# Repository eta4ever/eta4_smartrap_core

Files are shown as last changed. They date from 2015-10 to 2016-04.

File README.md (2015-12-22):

Ремикс, ремейк, форк, или как там это называется 3D-принтера Smartrap Core v.1.2 (https://www.youmagine.com/designs/smartcore). Основная идея - использование 15-миллиметрового алюминиевого квадрата в качестве рамы. 

Надо делать боковые стенки. Как минимум с боков, а лучше еще и сзади и снизу и вообще все закрывать. Или не надо, делаю откосины.

Что касается прошивки: взят релиз Marlin, актуальный на ноябрь 2015. Настроен на CoreXY, 190x190x190, по X и Y ремни GT2, на Z шпилька М5, экструдер МК8, все драйверы 1/16. Плюс Reprap Discount Full Graphic Controller.

Девайсина работает, обзор: http://3dtoday.ru/blogs/eta4ever/kubocore-my-variation-smartcore/

----------

2015-12-22

Корпус под плату, укладка проводов, фанерное дно, вулкан.
Обзор: http://3dtoday.ru/blogs/eta4ever/kubocore-part-3/

----------

2015-12-16

Направляющие Z на 110 мм, откосины на боковины по две штуки (профиль длиной 180 мм, угловые соединители 45.stl в Frame). Стало почти отлично.
Обзор доработок http://3dtoday.ru/blogs/eta4ever/kubocore-progress/

----------

2015-11-17

Соорудил стол на большой консоли. Стало лучше, но все равно хлипко. Надо шире расставлять направляющие (сейчас 60 мм, на консоли предусмотрено под 110 мм), а в идеале - делать направляющие с двух сторон. Но это гемор.

----------

2015-11-14

Реально печатная область сейчас получается 175х140 всего лишь. По Y в процессе доработки, будет побольше. Надо было длиннее раму делать, ну, поэкономил копеечный люминь, блин.

Напечатал новую консольку (Custom - Z - carriage), она монументальная. Пока что в процессе внедрения, примеряюсь к ней с уголками.

Ну и держалка для движка подачи пластика (Custom - extruder drive mount). А то надоело, что движок на стяжке болтается.

-----------

----------

Remix, remake or fork of Smartrap Core v.1.2 (https://www.youmagine.com/designs/smartcore).

----

Frame - уголки для сборки рамы из люминя.  Frame corners.

XY - переделанные крепления двигателей и роликов XY. Modified XY motors and rollers mounts. xy_left, xy_right, xy2_left_right

Z - переделанные детали Z. Под шпильку, из предыдущей версии Smartrap Core 1.01, с переделками под TR8x8. Modified Z parts, taken from previous 1.01 (threaded) version of Smartrap core, adapted for TR8x8 nut and bolt. z_carriage, z_top, z_bottom.

Unmodified - не затронутые переделками оригинальные детали, выгруженные из OpenJSCAD и пропущенные через netfabb для Slic3r. Untouched parts exported from OpenJSCAD and repaired in netfabb for Slic3r.

Алярма: Y Axis из Unmodified печатается с поддержкой, чтобы горизонтальные разрезы получились. Ну, они потом получаются, ножом и надфилем. Или можно стоя, но тоже с поддержкой под зажим линейного подшипника.

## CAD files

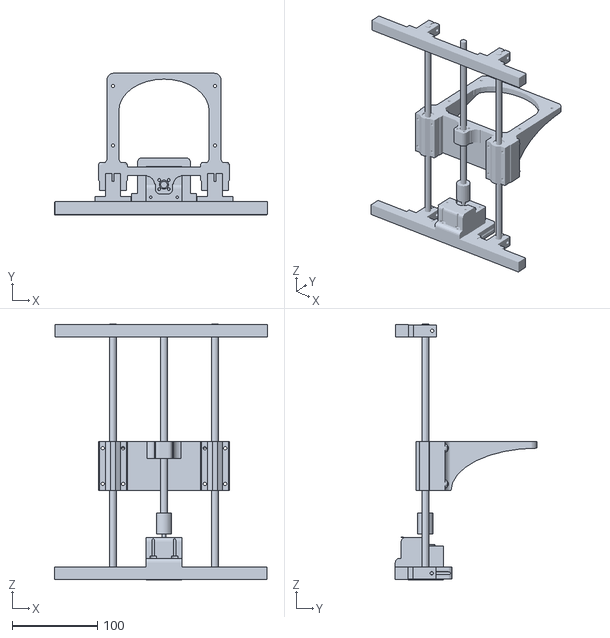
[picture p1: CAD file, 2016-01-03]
Custom/Z-experimental/z-assembly.stl
251.0 x 166.5 x 301.0

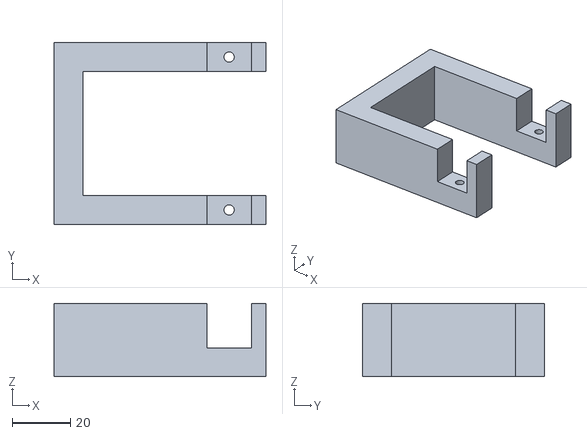
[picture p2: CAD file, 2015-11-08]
Custom/extruder drive mount.stl
72.5 x 62.3 x 25.0

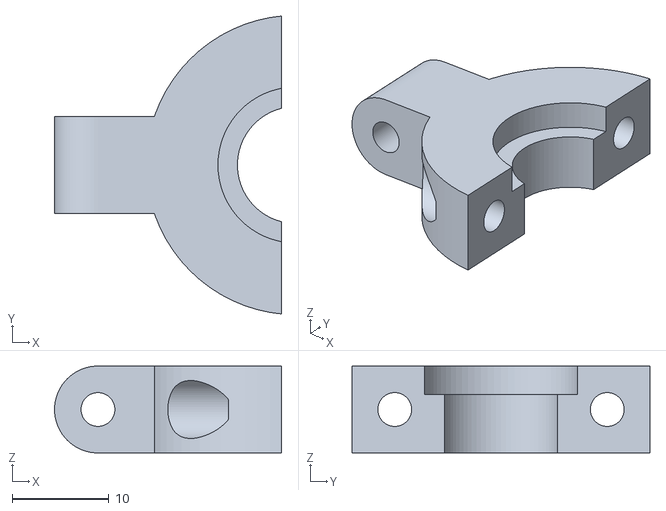
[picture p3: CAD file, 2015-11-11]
Custom/head/mount2_printable-only clip.stl
23.5 x 30.8 x 9.00

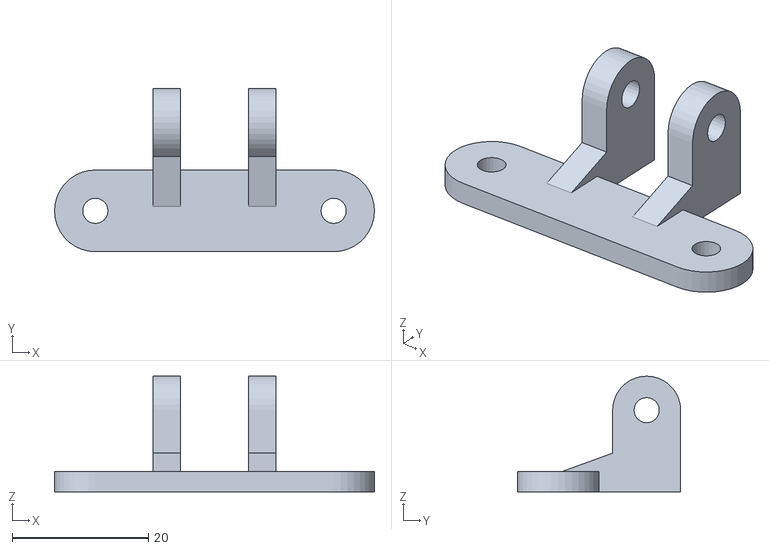
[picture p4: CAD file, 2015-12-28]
Custom/head/side_blower/side_blower_mount.stl
47.0 x 24.0 x 17.0

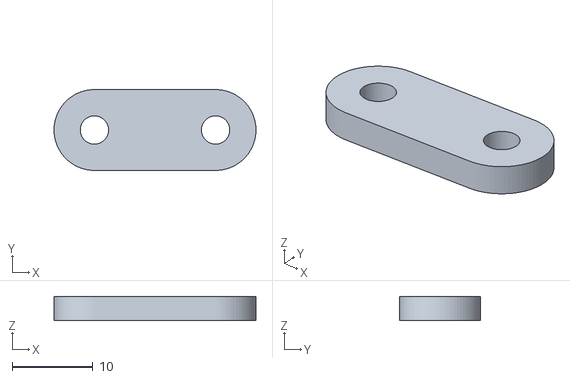
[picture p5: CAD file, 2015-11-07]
Custom/head/side_cooler_40mm/side_cooler_plank.stl
25.0 x 10.0 x 3.00

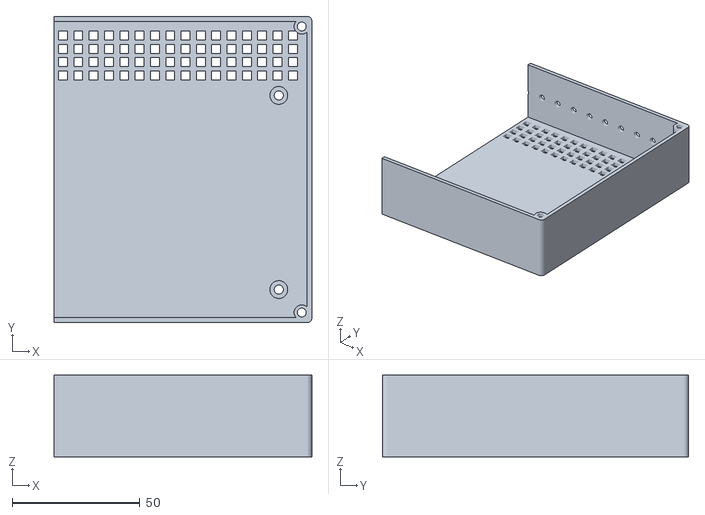
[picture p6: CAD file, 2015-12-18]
Custom/mks gen box/mks gen box1.stl
101.0 x 120.0 x 32.0

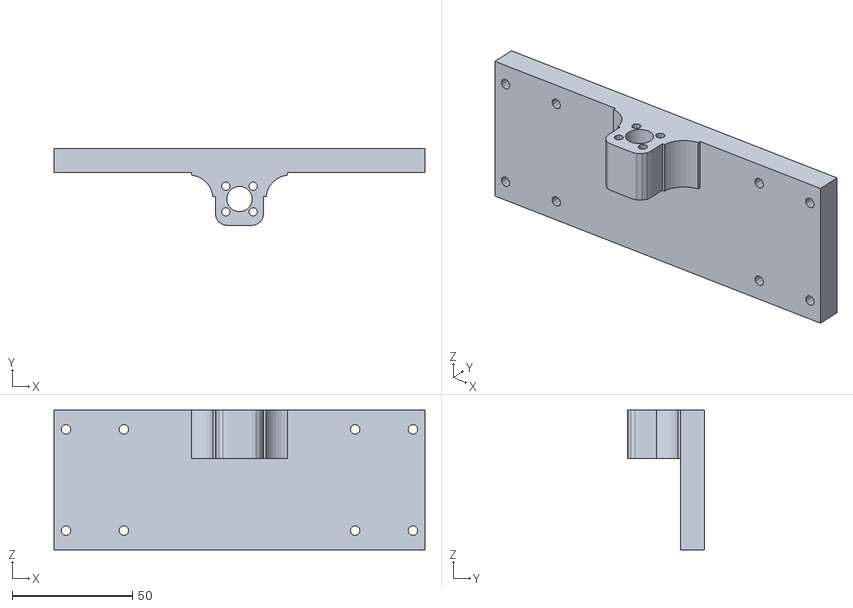
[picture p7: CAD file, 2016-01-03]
Custom/Z-experimental/z-plank.stl
154.0 x 32.0 x 58.0

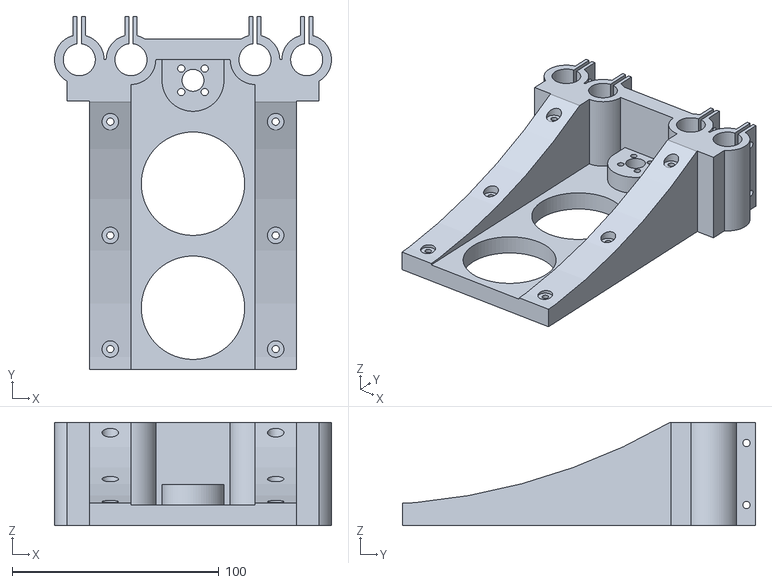
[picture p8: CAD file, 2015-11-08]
Custom/Z/carriage.stl
134.0 x 171.0 x 50.0

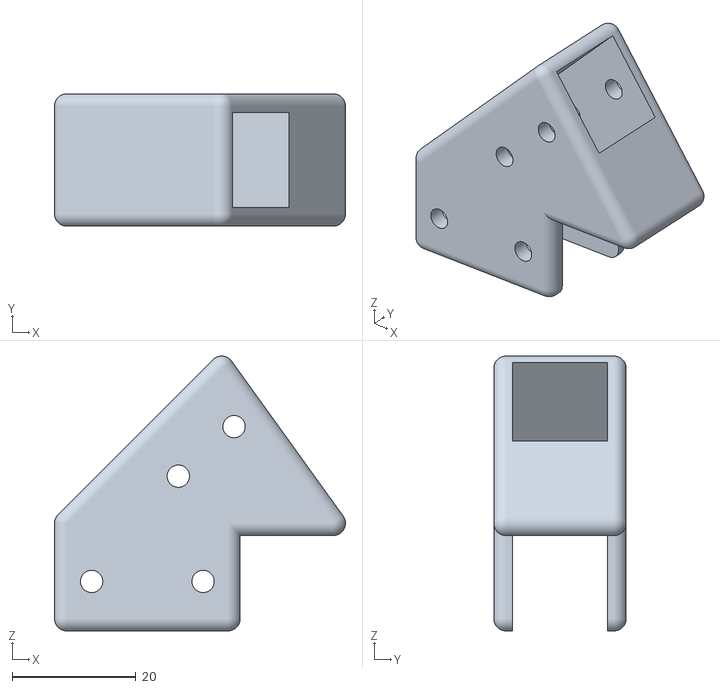
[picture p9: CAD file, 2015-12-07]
Frame/45.stl
47.0 x 21.4 x 44.4

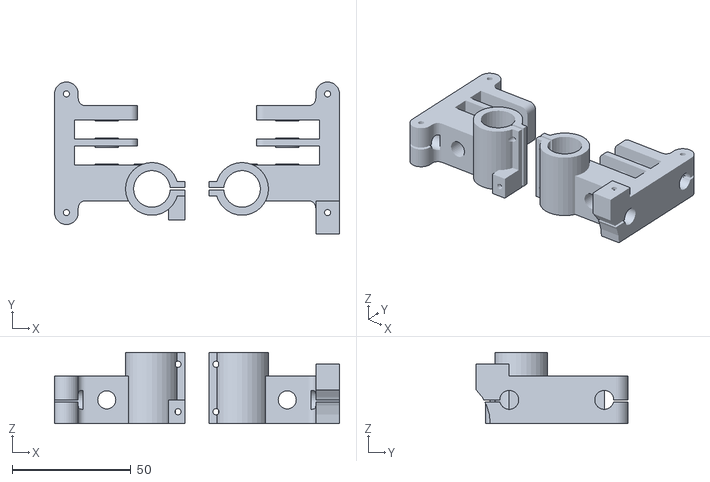
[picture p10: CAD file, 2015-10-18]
Unmodified/Y axis.stl
120.0 x 64.0 x 30.0

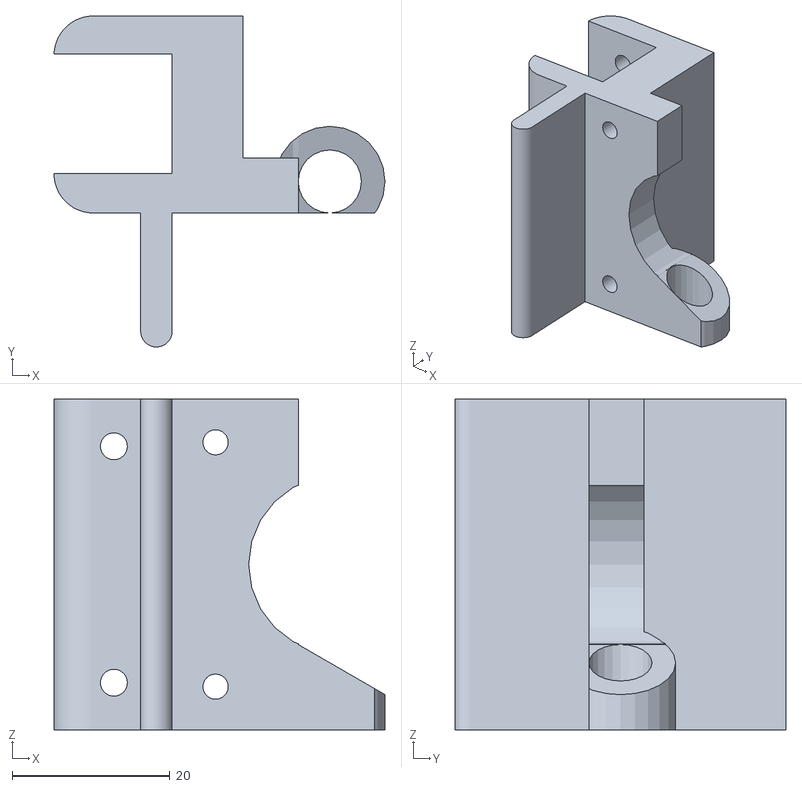
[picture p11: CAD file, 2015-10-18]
XY/xy_left.stl
42.0 x 42.0 x 42.0

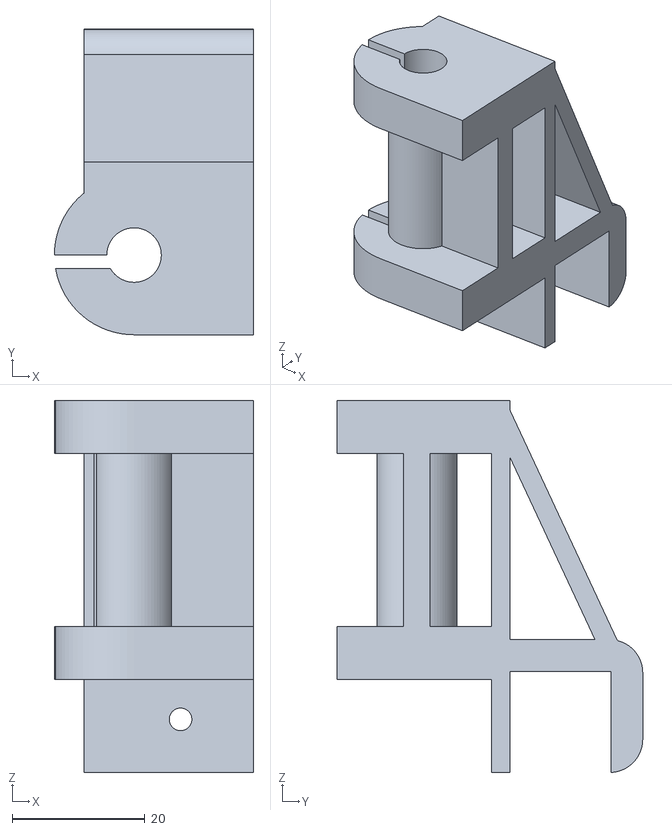
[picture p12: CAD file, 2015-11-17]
Z/Z_bottom_v2.stl
30.0 x 46.0 x 56.0

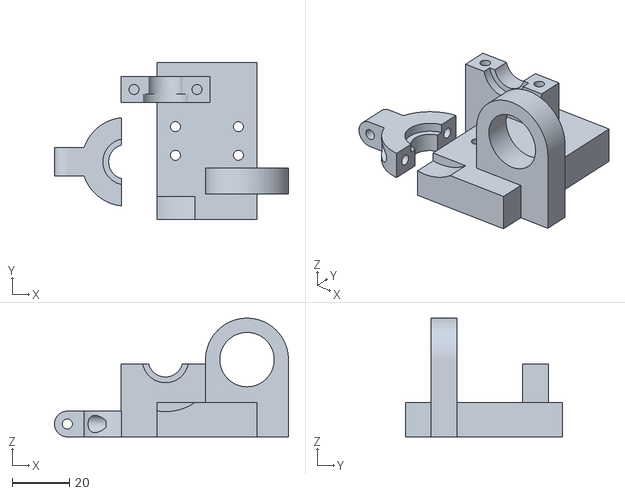
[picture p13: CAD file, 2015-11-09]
Custom/head/mount2_printable.stl
81.8 x 55.0 x 41.5

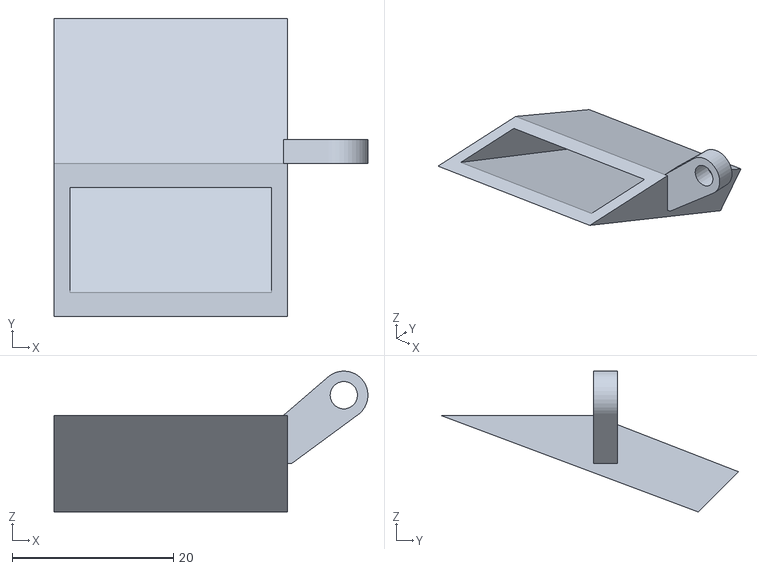
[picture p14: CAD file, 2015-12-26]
Custom/head/side_blower/side_blower_nozzle.stl
39.0 x 37.0 x 17.5

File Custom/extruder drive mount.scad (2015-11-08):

$fa=5; $fs=0.1;

module motor(){
	mwidth=42.3;
	mheight=40;
	difference(){
		union(){
			cube([mwidth, mwidth, mheight], center=true);
			translate([0, 0, mheight/2+1]) cylinder(h=2, r=11, center=true);
			translate([0, 0, mheight/2+12]) cylinder(h=24, r=2.5, center=true);
		}
		union(){
//			translate([-15.5, -15.5, mheight/2 - 2.25]) cylinder(h=4.51, r=1.5, center=true);
//			translate([-15.5, 15.5, mheight/2 - 2.25]) cylinder(h=4.51, r=1.5, center=true);
//			translate([15.5, -15.5, mheight/2 - 2.25]) cylinder(h=4.51, r=1.5, center=true);
//			translate([15.5, 15.5, mheight/2 - 2.25]) cylinder(h=4.51, r=1.5, center=true);
		}
	}//difference
}//module

mw=42.3;
prof=15.2;

rotate([0,90,0])
difference(){
	
	union(){
		translate([12.5-prof/2, 0, mw/2-5]) cube ([25, mw+20, mw+10], center=true);
		translate([12.5-prof/2, mw/2+5, mw+prof/2]) cube([25, 10, prof+10], center=true);
		translate([12.5-prof/2, -mw/2-5, mw+prof/2]) cube([25, 10, prof+10], center=true);
 	}
	
	union(){
		translate([0, 0, mw/2]) rotate([0,90,0]) color([0.6, 0, 0]) motor();
		translate([0, 0, mw+prof/2]) color([0,0.6,0]) cube([prof, 200, prof], center=true);

		translate([0, mw/2+5, mw+prof/2]) rotate([0, 90, 0]) cylinder(h=50, r=1.75, center=true);
		translate([0, -mw/2-5, mw+prof/2]) rotate([0, 90, 0]) cylinder(h=50, r=1.75, center=true);

	}
}

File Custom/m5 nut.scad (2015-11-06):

$fa=5; $fs=0.1;

module hexagon(in_diam, height) {
  cube_x = in_diam/1.75;
  for (r = [-60, 0, 60]) rotate([0,0,r]) cube([cube_x, in_diam, height], center=true);
}

// надо две штуки, низ и верх
difference(){
    hull(){
        translate([-5.5, -5.5, 0]) cylinder(h=4, r=4, center=true);
        translate([-5.5, 5.5, 0]) cylinder(h=4, r=4, center=true);
        translate([5.5, -5.5, 0]) cylinder(h=4, r=4, center=true);
        translate([5.5, 5.5, 0]) cylinder(h=4, r=4, center=true);
    }
    
    union(){
        // крепежные отверстия
        translate([-5.5, -5.5, 0]) cylinder(h=4.01, r=1.75, center=true);
        translate([-5.5, 5.5, 0]) cylinder(h=4.01, r=1.75, center=true);
        translate([5.5, -5.5, 0]) cylinder(h=4.01, r=1.75, center=true);
        translate([5.5, 5.5, 0]) cylinder(h=4.01, r=1.75, center=true);
        
        // под шпильку
        cylinder(h=4.01, r=2.75, center=true);
        
        // под гайку
        translate([0,0,1]) hexagon(8.2, 2.01);
    }
}

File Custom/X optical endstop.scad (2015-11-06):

$fa=5; $fs=0.1;

cube([30, 5, 1.5]);
cube([10, 16, 1.5]);
translate([0, 14.5, 0]) cube ([10, 1.5, 18]);

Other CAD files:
Custom/head/side_cooler_40mm/side_cooler.stl
Custom/mks gen box/mks gen box2.stl
Custom/Z optical endstop.stl
Frame/corner.stl
Custom/Y optical endstop.scad
Custom/X optical endstop.stl
Custom/Y optical endstop.stl
Custom/Z optical endstop.scad
Custom/Z-experimental/z-console.stl
Custom/Z-experimental/z-motor-1.stl
Custom/Z-experimental/z-motor-2.stl
Custom/Z-experimental/z-sc8luu.stl
Custom/Z-experimental/z-sk8.stl
Custom/Z/carriage.scad
Custom/head/e3dv6 simple.scad
Custom/head/fan_mount.stl
Custom/head/mount.scad
Custom/head/mount.stl
Custom/head/side_blower/side_blower_mount.scad
Custom/head/side_blower/side_blower_nozzle.scad
Custom/head/side_cooler_40mm/side_cooler.scad
Custom/head/side_cooler_40mm/side_cooler_plank.scad
Custom/m5 nut.stl
Custom/mks gen box/mks gen box cover.scad
Custom/mks gen box/mks gen box cover.stl
Custom/mks gen box/mks gen box holder.scad
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

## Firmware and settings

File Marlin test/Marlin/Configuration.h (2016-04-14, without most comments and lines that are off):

#define CONFIGURATION_H
#include "boards.h"
#define STRING_VERSION_CONFIG_H __DATE__ " " __TIME__ // build date and time
#define STRING_CONFIG_H_AUTHOR "(none, default config)" // Who made the changes.
#define SERIAL_PORT 0
#define BAUDRATE 115200
#define MOTHERBOARD 33
#define EXTRUDERS 1
#define POWER_SUPPLY 1
#define TEMP_SENSOR_0 1
#define TEMP_SENSOR_1 0
#define TEMP_SENSOR_2 0
#define TEMP_SENSOR_BED 1
#define MAX_REDUNDANT_TEMP_SENSOR_DIFF 10
#define TEMP_RESIDENCY_TIME 10  // (seconds)
#define TEMP_HYSTERESIS 3       // (degC) range of +/- temperatures considered "close" to the target one
#define TEMP_WINDOW     1       // (degC) Window around target to start the residency timer x degC early.
#define HEATER_0_MINTEMP 0
#define HEATER_1_MINTEMP 0
#define HEATER_2_MINTEMP 0
#define BED_MINTEMP 0
#define HEATER_0_MAXTEMP 275
#define HEATER_1_MAXTEMP 275
#define HEATER_2_MAXTEMP 275
#define BED_MAXTEMP 150
#define PIDTEMP
#define BANG_MAX 255 // limits current to nozzle while in bang-bang mode; 255=full current
#define PID_MAX BANG_MAX // limits current to nozzle while PID is active (see PID_FUNCTIONAL_RANGE below); 255=full current
  #define PID_FUNCTIONAL_RANGE 10 // If the temperature difference between the target temperature and the actual temperature
  #define PID_INTEGRAL_DRIVE_MAX PID_MAX  //limit for the integral term
  #define K1 0.95 //smoothing factor within the PID
  #define PID_dT ((OVERSAMPLENR * 10.0)/(F_CPU / 64.0 / 256.0)) //sampling period of the temperature routine
    #define  DEFAULT_Kp 22.2
    #define  DEFAULT_Ki 1.08
    #define  DEFAULT_Kd 114
#define MAX_BED_POWER 255 // limits duty cycle to bed; 255=full current
#define PREVENT_DANGEROUS_EXTRUDE
#define PREVENT_LENGTHY_EXTRUDE
#define EXTRUDE_MINTEMP 170
#define EXTRUDE_MAXLENGTH (X_MAX_LENGTH+Y_MAX_LENGTH) //prevent extrusion of very large distances.
#define COREXY
#define ENDSTOPPULLUPS // Comment this out (using // at the start of the line) to disable the endstop pullup resistors
  #define ENDSTOPPULLUP_XMAX
  #define ENDSTOPPULLUP_YMAX
  #define ENDSTOPPULLUP_ZMAX
  #define ENDSTOPPULLUP_XMIN
  #define ENDSTOPPULLUP_YMIN
  #define ENDSTOPPULLUP_ZMIN
const bool X_MIN_ENDSTOP_INVERTING = false; // set to true to invert the logic of the endstop.
const bool Y_MIN_ENDSTOP_INVERTING = false; // set to true to invert the logic of the endstop.
const bool Z_MIN_ENDSTOP_INVERTING = true; // set to true to invert the logic of the endstop.
const bool X_MAX_ENDSTOP_INVERTING = true; // set to true to invert the logic of the endstop.
const bool Y_MAX_ENDSTOP_INVERTING = true; // set to true to invert the logic of the endstop.
const bool Z_MAX_ENDSTOP_INVERTING = true; // set to true to invert the logic of the endstop.
#if defined(COREXY) && !defined(DISABLE_MAX_ENDSTOPS)
  #define DISABLE_MAX_ENDSTOPS
#endif
#define X_ENABLE_ON 0
#define Y_ENABLE_ON 0
#define Z_ENABLE_ON 0
#define E_ENABLE_ON 0 // For all extruders
#define DISABLE_X false
#define DISABLE_Y false
#define DISABLE_Z false
#define DISABLE_E false // For all extruders
#define DISABLE_INACTIVE_EXTRUDER true //disable only inactive extruders and keep active extruder enabled
#define INVERT_X_DIR true    // for Mendel set to false, for Orca set to true
#define INVERT_Y_DIR true    // for Mendel set to true, for Orca set to false
#define INVERT_Z_DIR true     // for Mendel set to false, for Orca set to true
#define INVERT_E0_DIR true   // for direct drive extruder v9 set to true, for geared extruder set to false
#define INVERT_E1_DIR false    // for direct drive extruder v9 set to true, for geared extruder set to false
#define INVERT_E2_DIR false   // for direct drive extruder v9 set to true, for geared extruder set to false
#define X_HOME_DIR -1
#define Y_HOME_DIR -1
#define Z_HOME_DIR -1
#define min_software_endstops false // If true, axis won't move to coordinates less than HOME_POS.
#define max_software_endstops false  // If true, axis won't move to coordinates greater than the defined lengths below.
#define X_MAX_POS 190
#define X_MIN_POS 0
#define Y_MAX_POS 190
#define Y_MIN_POS 0
#define Z_MAX_POS 190
#define Z_MIN_POS 0
#define X_MAX_LENGTH (X_MAX_POS - X_MIN_POS)
#define Y_MAX_LENGTH (Y_MAX_POS - Y_MIN_POS)
#define Z_MAX_LENGTH (Z_MAX_POS - Z_MIN_POS)
#define Z_PROBE_REPEATABILITY_TEST  // If not commented out, Z-Probe Repeatability test will be included if Auto Bed Leveling is Enabled.
#define MANUAL_X_HOME_POS 0
#define MANUAL_Y_HOME_POS 0
#define MANUAL_Z_HOME_POS 0
#define NUM_AXIS 4 // The axis order in all axis related arrays is X, Y, Z, E
#define HOMING_FEEDRATE {50*60, 50*60, 4*60, 0}  // set the homing speeds (mm/min)
#define DEFAULT_AXIS_STEPS_PER_UNIT   {160,160,400,100} // TR8x8 // 1/32 xy
#define DEFAULT_MAX_FEEDRATE          {1000, 1000, 2.5, 100}
#define DEFAULT_MAX_ACCELERATION      {1000,1000,100,1000}
#define DEFAULT_ACCELERATION          2000    // X, Y, Z and E max acceleration in mm/s^2 for printing moves
#define DEFAULT_RETRACT_ACCELERATION  2000   // X, Y, Z and E max acceleration in mm/s^2 for retracts
#define DEFAULT_XYJERK                20.0    // (mm/sec)
#define DEFAULT_ZJERK                 10.0     // (mm/sec)
#define DEFAULT_EJERK                 5.0    // (mm/sec)
#define CUSTOM_M_CODES
  #define CUSTOM_M_CODE_SET_Z_PROBE_OFFSET 851
  #define Z_PROBE_OFFSET_RANGE_MIN -5
  #define Z_PROBE_OFFSET_RANGE_MAX 0
#define PLA_PREHEAT_HOTEND_TEMP 180
#define PLA_PREHEAT_HPB_TEMP 70
#define PLA_PREHEAT_FAN_SPEED 255   // Insert Value between 0 and 255
#define ABS_PREHEAT_HOTEND_TEMP 240
#define ABS_PREHEAT_HPB_TEMP 100
#define ABS_PREHEAT_FAN_SPEED 255   // Insert Value between 0 and 255
#define ENCODER_PULSES_PER_STEP 1 // Increase if you have a high resolution encoder
#define ENCODER_STEPS_PER_MENU_ITEM 4 // Set according to ENCODER_PULSES_PER_STEP or your liking
#define REPRAP_DISCOUNT_SMART_CONTROLLER
 #define ULTIPANEL
 #define NEWPANEL
  #define SDSUPPORT
  #define ULTRA_LCD
    #define LCD_WIDTH 20
    #define LCD_HEIGHT 4
#define SOFT_PWM_SCALE 0
#define FILAMENT_SENSOR_EXTRUDER_NUM	0  //The number of the extruder that has the filament sensor (0,1,2)
#define MEASUREMENT_DELAY_CM			14  //measurement delay in cm.  This is the distance from filament sensor to middle of barrel
#define DEFAULT_NOMINAL_FILAMENT_DIA  3.0  //Enter the diameter (in mm) of the filament generally used (3.0 mm or 1.75 mm) - this is then used in the slicer software.  Used for sensor reading validation
#define MEASURED_UPPER_LIMIT          3.30  //upper limit factor used for sensor reading validation in mm
#define MEASURED_LOWER_LIMIT          1.90  //lower limit factor for sensor reading validation in mm
#define MAX_MEASUREMENT_DELAY			20  //delay buffer size in bytes (1 byte = 1cm)- limits maximum measurement delay allowable (must be larger than MEASUREMENT_DELAY_CM  and lower number saves RAM)
#define DEFAULT_MEASURED_FILAMENT_DIA  DEFAULT_NOMINAL_FILAMENT_DIA  //set measured to nominal initially
#include "Configuration_adv.h"
#include "thermistortables.h"

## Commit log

2015-10-17 first
    Вытащено в отдельную репу
    [corner.scad, corner.stl, xy1.stl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]
2015-10-17 xy2 (rollers) mounts (right/left symmetric)
    [xy2.stl, xy2_left_right.scad, xy2_left_right.stl]
2015-10-17 unmodified parts added
    [Y axis.stl]
2015-10-18 Z bottom
    [Z_bottom.scad, Z_bottom.stl, Z_bottom_orig.stl]
2015-10-18 added commented motor to xy_left
    [xy_left.scad, xy_left.stl]
2015-10-18 Z top
    [Z_top.scad, Z_top.stl, Z_top_orig.stl]
2015-10-18 rotated for print
    [Y axis.stl, Z_bottom.stl, Z_top.stl]
2015-10-20 заметка по профилю и валам
2015-10-21 скорректированы профиль и валы
2015-10-28 торчалки для оптических выключаетелей
    [X optical endstop.scad, X optical endstop.stl, Y optical endstop.scad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]
2015-10-29 5mm nut holder
    [Z optical endstop.scad, Z optical endstop.stl, m5 nut.scad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]
2015-11-06 encoder steps fixed
    [Configuration.h]
2015-11-07 custom head
    [e3dv6 simple.scad, mount.scad]
2015-11-07 fan mount
    [fan_mount.STL]
2015-11-08 custom z carriage
    [carriage.scad]
2015-11-08 z carriage
    [carriage.scad, carriage.stl]
2015-11-08 архив
    [Z_carriage.scad, Z_carriage.stl, Z_carriage_orig.stl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]
2015-11-08 fixed custom z carriage
    [Z_carriage.scad, Z_carriage.stl, Z_carriage_orig.stl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]
2015-11-08 extruder drive mount
    [extruder drive mount.scad, extruder drive mount.stl]
2015-11-08 driva mount
    [extruder drive mount.scad]
2015-11-09 mount printable stl
    [mount2_printable.stl]
2015-11-11 инвертирован концевик z для индуктивного
    [Configuration.h, mount2_printable-only clip.stl]
2015-11-11 немного допиливаний для репрап дисконт фулграфика
    [Configuration.h]
2015-11-17 z top add to 110mm
    [Z_top_v2.scad, Z_top_v2.stl]
2015-11-17 ухи Z верх принтабельные
    [Z_top_v2_printable.stl]
2015-11-17 Z нижние доп.ухи
    [Z_bottom_v2.scad, Z_bottom_v2.stl, Z_bottom_v2_printable.stl]
2015-12-07 45 упор
    [45.scad, 45.stl]
2015-12-15 mks gen box
    [mks gen box.scad]
2015-12-15 upd box - usb
    [mks gen box.scad, mks gen box.stl]
2015-12-18 rotated cut box
    [mks gen box1.stl, mks gen box2.stl]
2015-12-25 side cooler side blower
    [side_blower_mount.scad, side_blower_mount.stl, side_blower_nozzle.scad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]
2015-12-25 side blower
    [side_blower_mount.scad]
2015-12-28 доработка кронштейна обдува
    [side_blower_mount.scad, side_blower_mount.stl]
2016-01-02 freecad experiments
    [freecad-test.fcstd, test.stl]
2016-01-03 z tinker
    [z-assembly.stl, z-motor-2.stl, z-sk8.stl]
2016-01-10 marlin test dontuze
    [Configuration.h, Configuration_adv.h]
2016-01-12 marlin test serial 2
    [Configuration.h]
2016-04-14 заметко
